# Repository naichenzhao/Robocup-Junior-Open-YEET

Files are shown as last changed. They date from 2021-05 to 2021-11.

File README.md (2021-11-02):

**Robocup Junior YEET**

These are the robot designs I created for Robocup Junior Open weight. 

These are my own creations and since I have graduated from the event, anyone rteading this is free to build off of any of my designs. My hope for this is to inspire others to build off of what I haev and use them to create even better concepts for the competition.

If you have any questions or concerns regarding the design, feel free to contact me:
- Twitter: https://twitter.com/N_zhao_
- Discord: https://discord.gg/ySBR4mmBkV

Included in the repo are:
- My 2020 design I planned on using for that year's competition - This is mostly tested but never created
- My 2021 design Which is pureley theoretical. It is a modefied version of the 2020 design built around a 20cm diameter

**2020 Design:**
This is the robot I planned on using for the 2020 competition (Which was cancelled due to covid). Some parts of the robot were tested but it was never completed as production stopped when the competition was cancelled

The specs of the robot are:
- 2x Teensy 4.0
- 1x Teensy 3.5
- 1x Open MV H7 (Omnidirectional mirror)
- 1x Spinning LIDAR
- 1x Bluetooth module
- 1x BNO-055 Accelerometer
- 2x Dribbler
- 2x Directional Kicker (I created models using both slider and geneva methods)
- 32x Photoresistors w/ LEDs (Controlled by 2 multiplexers)
- 12x Buttons w/ LEDs
- 2x IR laser module

**2021 Design:**
This is a robot built for the 2021 competition but since there is a significant chance that the competition will be cancalled, I have decided to thus release all of the robot files. This design is a smaller version built around the 2020 design created around a 20cm diameter instead of a 22 cm diameter

The specs of the robot are:
- 2x Teensy 4.0
- 1x Teensy 4.1
- 1x Open MV H7 (Omnidirectional mirror)
- 1x Spinning LIDAR
- 1x Bluetooth module
- 1x BNO-055 Accelerometer
- 2x Dribbler
- 2x Kicker
- 32x Photoresistors w/ LEDs (Controlled by 2 multiplexers)
- 8x Buttons w/ LEDs (Intead of individual LEDs, I am using a neopixel strip to conserve pins)
- 2x IR laser module

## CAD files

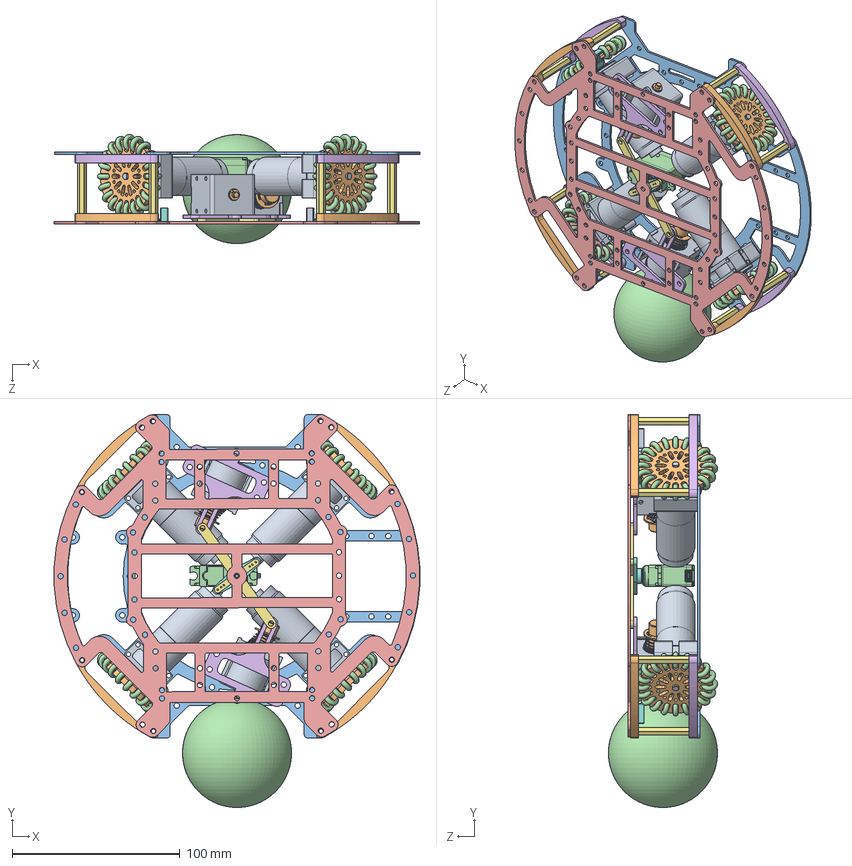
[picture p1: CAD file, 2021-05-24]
2020/Aimbot/Aimbot Test.SLDASM
217.9 x 234.3 x 65.1 mm
Open Motor x 4
50全向轮毂1 x 4
50全向轮小轴 x 80
50全向轮小轮 x 80
50全向轮毂2 x 4
Wheel Guard 4 x 4
M3X30-SCu x 8
Laser Left NH x 2
Laser Right NH x 2
Wheel Guard 5 x 4
Bot
球
Aimbot Mid
Aimbot Swing x 2
Aimbot Lever
Sero Adaptor
Part5^w_cb1029A x 2
Part1^w_cb1029A_pl x 2
w_21053081 x 2
Servo 2

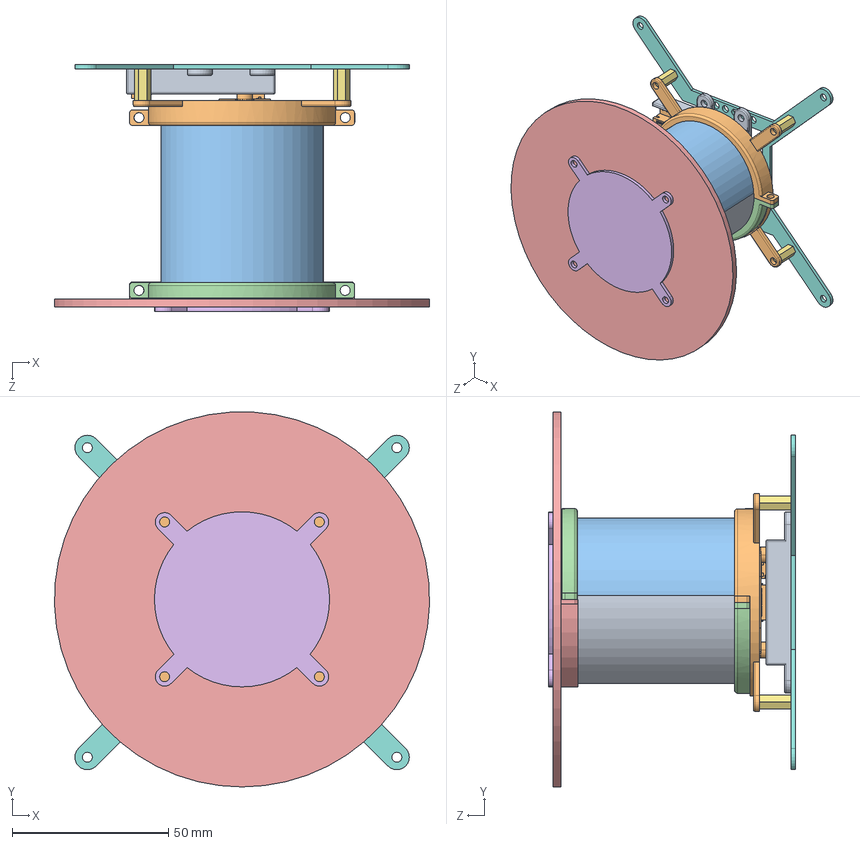
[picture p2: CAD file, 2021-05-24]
2021/Camera/Camera Module.SLDASM
119.9 x 119.9 x 79.0 mm
DCam 2
Open MV
镜筒
camera lock x 2
NH Top Cover V5
Mirror Adaptor
10mm Standoff x 4
Open Cam 1 - V2
Tube
Open Cam 2

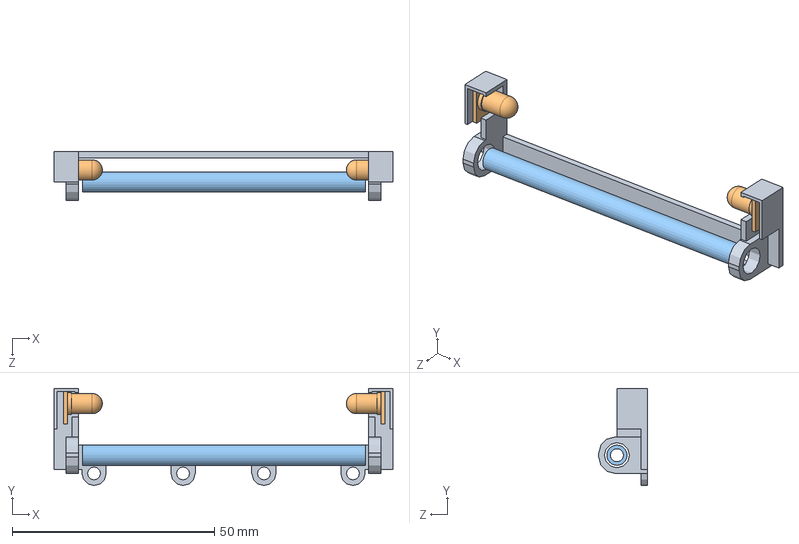
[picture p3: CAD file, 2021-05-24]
2021/Laser Module/Laser-Roller Assembly.SLDASM
83.8 x 24.0 x 12.0 mm
Laser - Roller module
IR Laser Diode x 2
Roller Bar

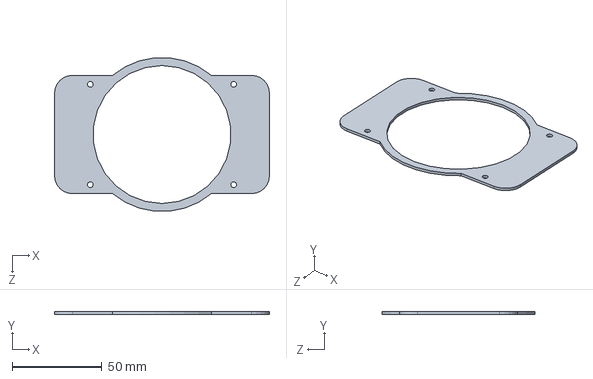
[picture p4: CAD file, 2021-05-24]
2021/PCB - Solidworks/Main PCB.SLDPRT
120.0 x 1.50 x 85.6 mm

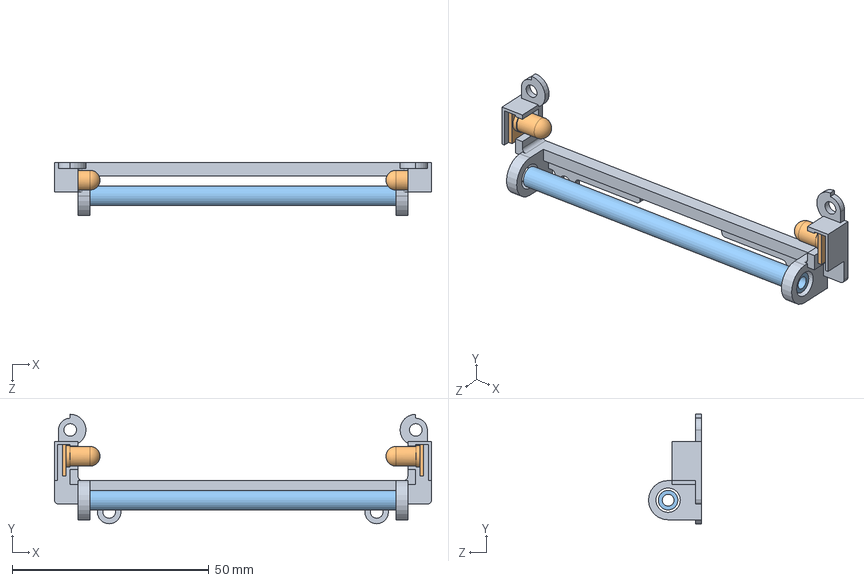
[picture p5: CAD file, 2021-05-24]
2020/Laser Module/Laser + Roller Assembly.SLDASM
95.8 x 27.9 x 13.5 mm
Laser Module
IR Laser Diode x 2
Roller Rod

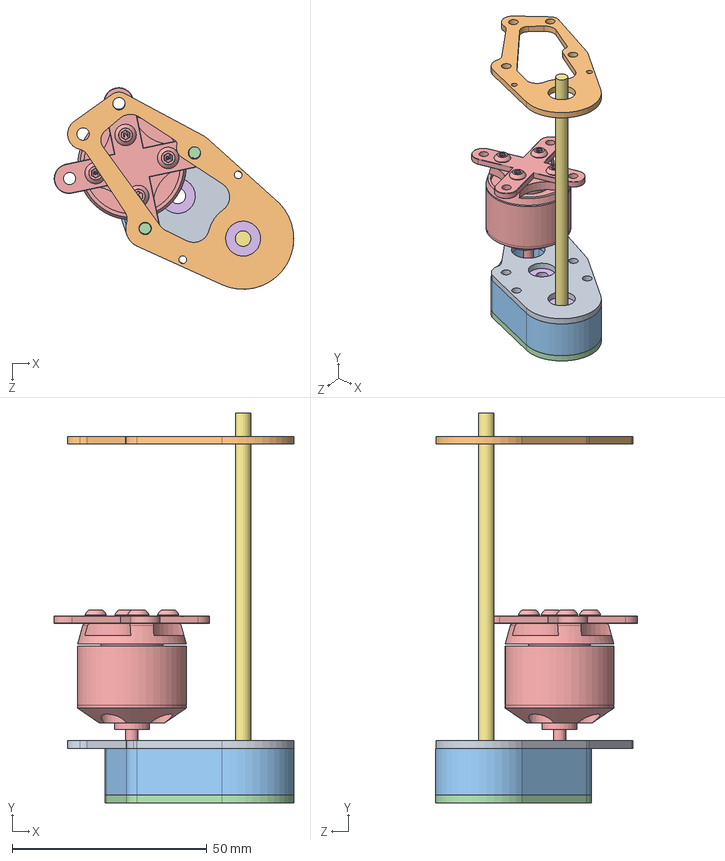
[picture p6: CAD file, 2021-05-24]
2020/Dribbler/Dribbler200.SLDASM
61.4 x 100.0 x 51.7 mm
Dribbler 201
Dribbler 202
Dribbler 203
Dribbler 204
Motor
Large Gear x 2
Dribbler Rod

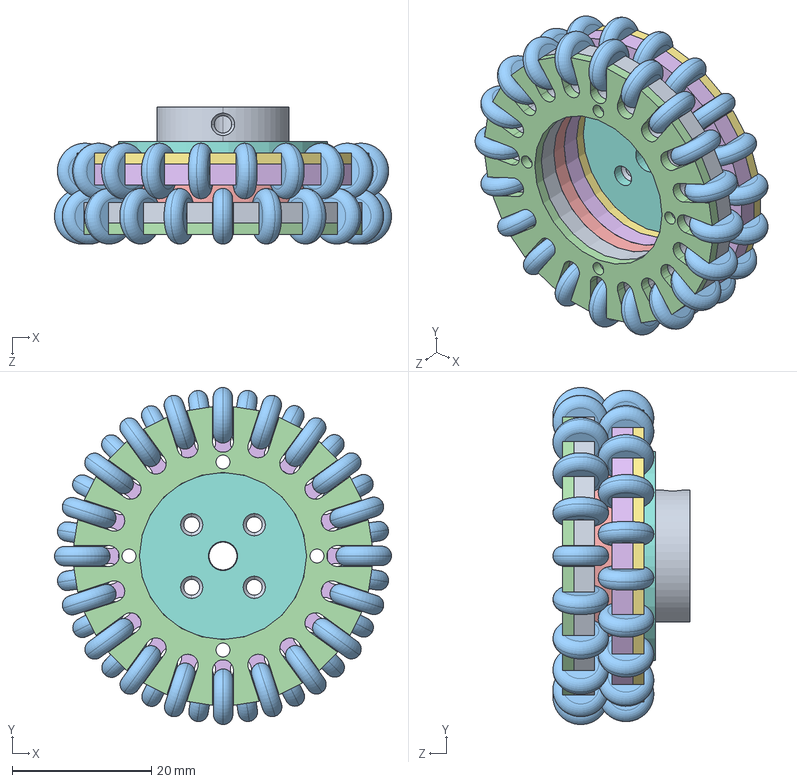
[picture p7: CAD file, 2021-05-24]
2020/Wheel/Wheel 2.0.SLDASM
48.4 x 48.4 x 19.7 mm
Wheel Plate 2.2
Wheel 2.0 Ring x 2
Inner Wheel - GTF x 40
Wheel Plate 2.1
Spacer 2.0
Wheel Plate 2.4
Wheel Plate 2.3
Cross 2.0
Wheel Mounting

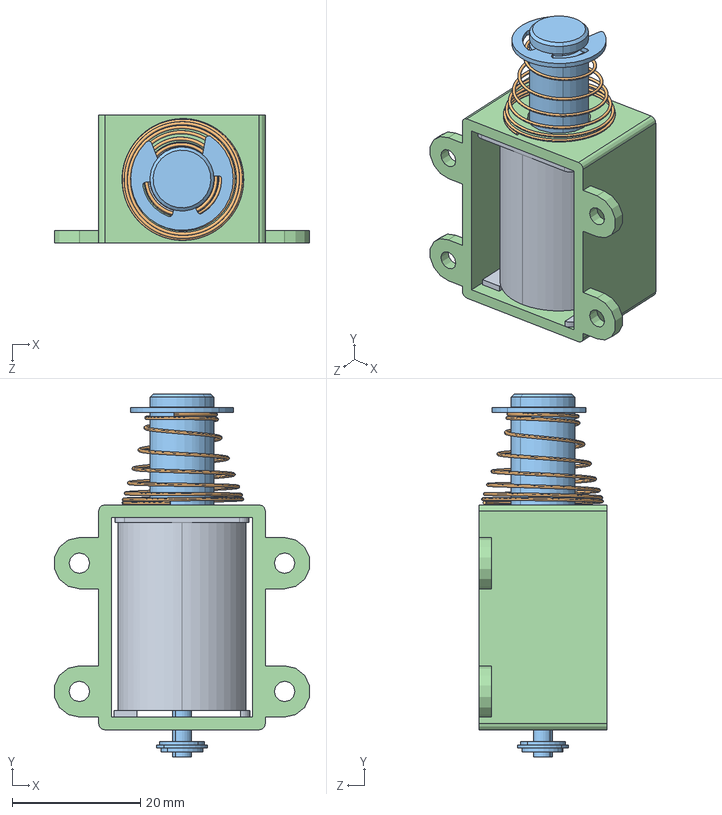
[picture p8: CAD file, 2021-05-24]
2021/New Kicker/Kicker Assembly.SLDASM
39.8 x 56.6 x 20.0 mm
Kicker Solenoid Core
Kicker Spring
Kicker Core
kicker Shell

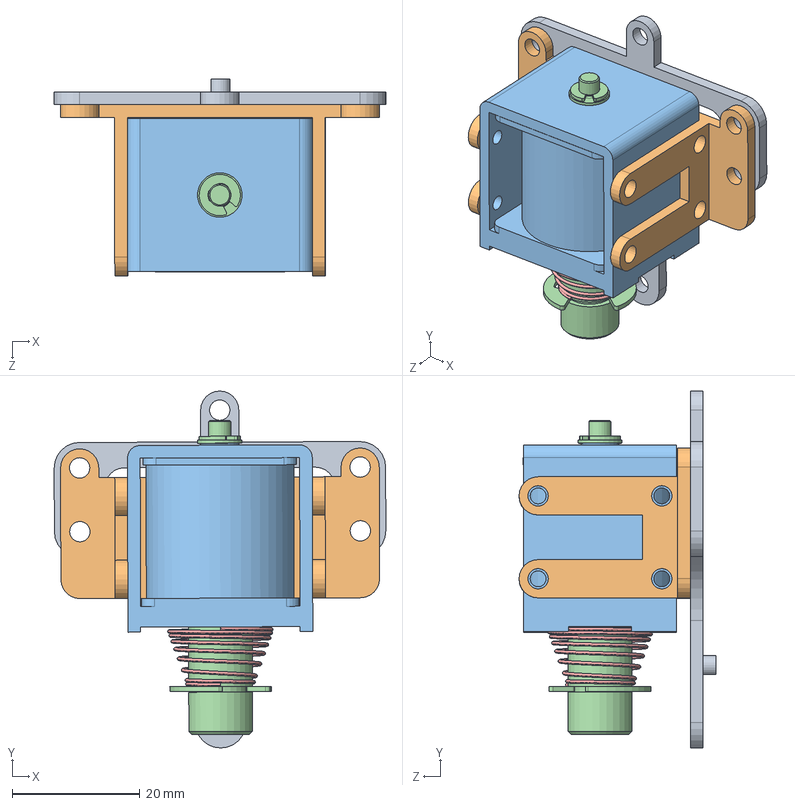
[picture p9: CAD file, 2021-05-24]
2020/Aimbot/Aimbot-S Swing.SLDASM
52.0 x 56.0 x 30.9 mm
Aimbot Swing
CB1029 Kicker Stand
Part5^w_cb1029A
Part1^w_cb1029A_pl
w_21053081

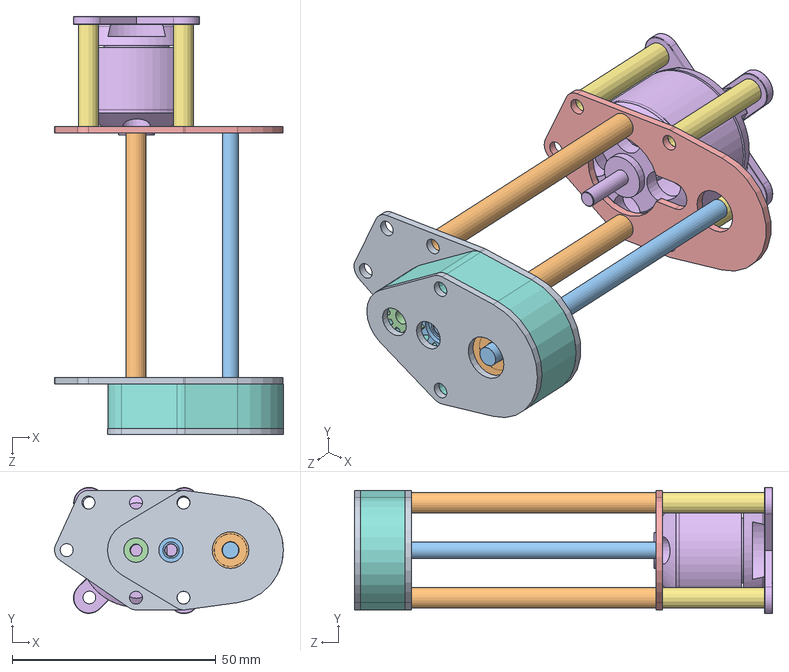
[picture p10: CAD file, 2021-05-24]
2021/Mini Dribbler/Mini Dribbler Assembly.SLDASM
56.2 x 31.0 x 102.7 mm
Mini Dribbler Plate 1
front - Gear
mid-gear
BrushlessGear
Mini Dribbler Plate3
Stand
25mm - pole x 3
Mini Dribbler wall
Mini Dribbler Plate 2
60mm - pole x 2
Rod

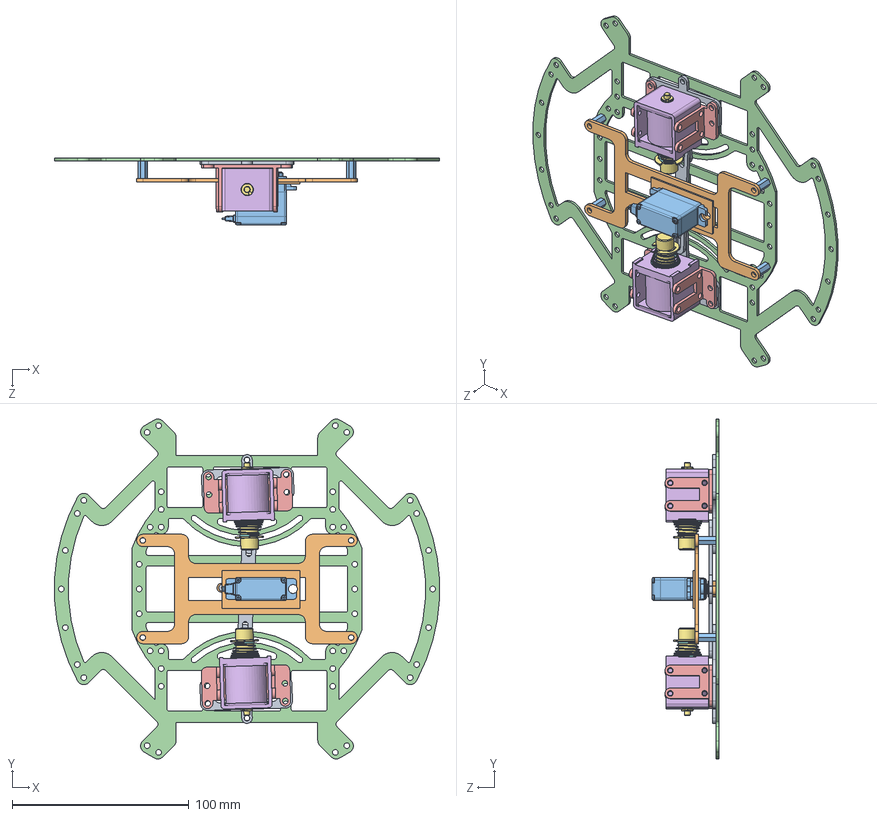
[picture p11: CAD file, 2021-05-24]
2020/Aimbot/Aimbot-S Test.SLDASM
217.7 x 192.2 x 37.6 mm
Aimbot Swing x 2
Sero Adaptor
Servo 2
Aimbot Mid
CB1029 Kicker Stand x 2
Part5^w_cb1029A x 2
Part1^w_cb1029A_pl x 2
w_21053081 x 2
Aimbot Lever
Servo Stand
10mm Standoff x 4

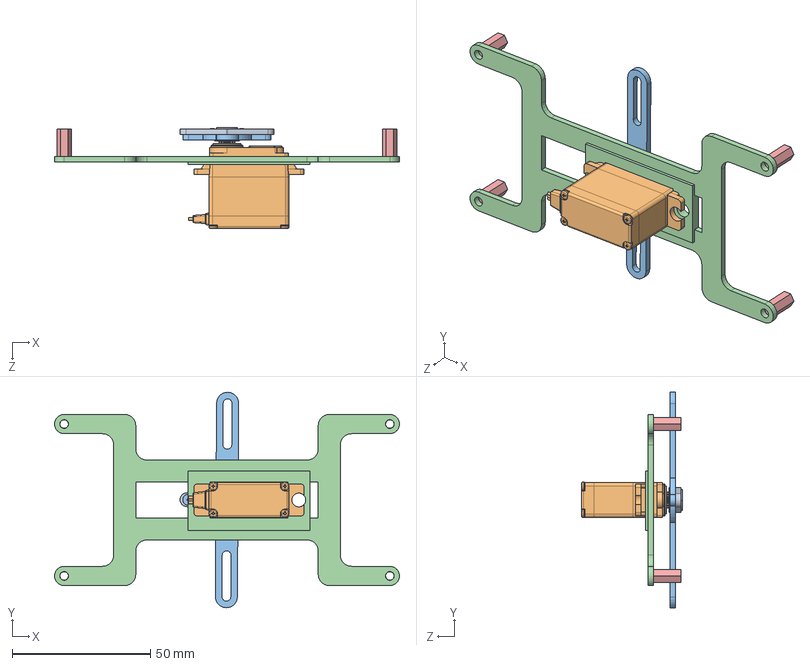
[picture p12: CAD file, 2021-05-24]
2020/Aimbot/Aimbot-S Pivot.SLDASM
124.8 x 78.0 x 36.6 mm
Sero Adaptor
Servo 2
Aimbot Lever
Servo Stand
10mm Standoff x 4

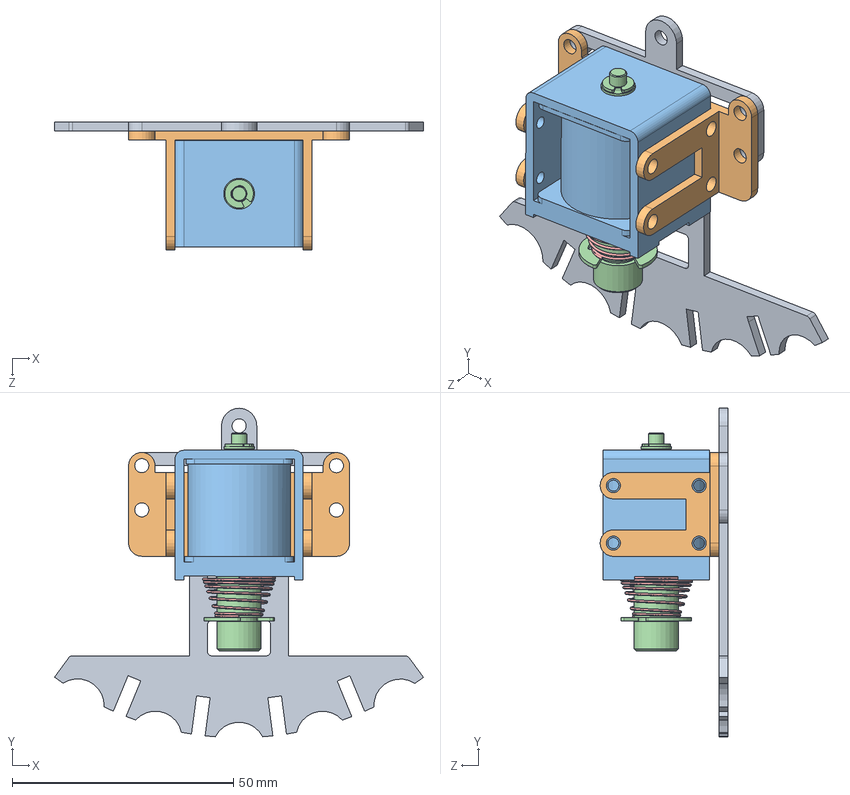
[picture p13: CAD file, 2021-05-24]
2020/Aimbot/Aimbot-G Swing.SLDASM
83.4 x 74.3 x 28.9 mm
Aimbot Geneva 1
CB1029 Kicker Stand
Part5^w_cb1029A
Part1^w_cb1029A_pl
w_21053081

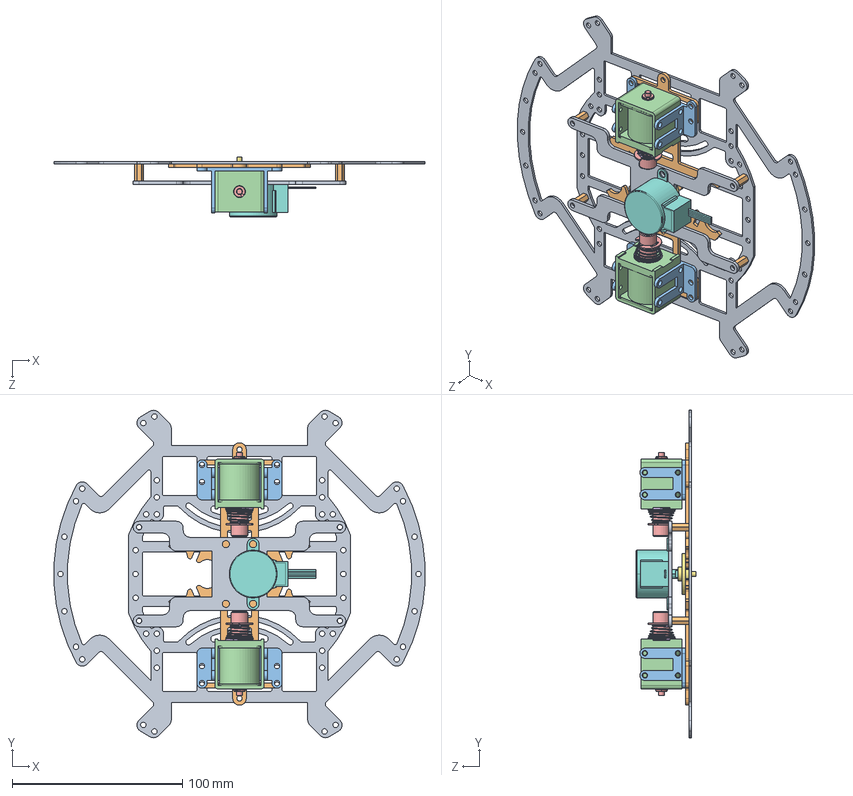
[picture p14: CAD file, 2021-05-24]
2020/Aimbot/Aimbot-G Test.SLDASM
217.7 x 192.2 x 35.0 mm
Aimbot Mid
Aimbot Geneva 1 x 2
CB1029 Kicker Stand x 2
Part5^w_cb1029A x 2
Part1^w_cb1029A_pl x 2
w_21053081 x 2
Aimbot Geneva 2
Stepper Motor
Stepper Stand
10mm Standoff x 4

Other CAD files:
2021/Wheel/Wheel 2.0.SLDASM
2020/Aimbot/Aimbot-G Pivot.SLDASM
2020/Camera/NH Top Cover V5.SLDPRT
2020/Aimbot/Aimbot Geneva 1.SLDPRT
2020/Aimbot/Aimbot Geneva 2.SLDPRT
2020/Aimbot/Aimbot Lever V2.SLDPRT
2020/Aimbot/Aimbot Lever.SLDPRT
2020/Aimbot/Aimbot Mid.SLDPRT
2020/Aimbot/Aimbot Swing + Kicker.SLDPRT
2020/Aimbot/Aimbot Swing.SLDPRT
2020/Aimbot/Sero Adaptor.SLDPRT
2020/Aimbot/Servo 2.SLDPRT
2020/Aimbot/Servo Stand V2.SLDPRT
2020/Aimbot/Servo Stand.SLDPRT
2020/Aimbot/Servo.SLDPRT
2020/Aimbot/Stepper Motor.SLDPRT
2020/Aimbot/Stepper Stand.SLDPRT
2020/Camera/Mirror Adaptor.SLDPRT
2020/Camera/Open Cam 1 - V2.SLDPRT
2020/Camera/Open Cam 1.SLDPRT
2020/Camera/Open Cam 2.SLDPRT
2020/Camera/Tube.SLDPRT
2020/Camera/camera lock.SLDPRT
2020/Dribbler/Dribbler 201.SLDPRT
2020/Dribbler/Dribbler 202.SLDPRT
2020/Dribbler/Dribbler 203.SLDPRT
2020/Dribbler/Dribbler 204.SLDPRT
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

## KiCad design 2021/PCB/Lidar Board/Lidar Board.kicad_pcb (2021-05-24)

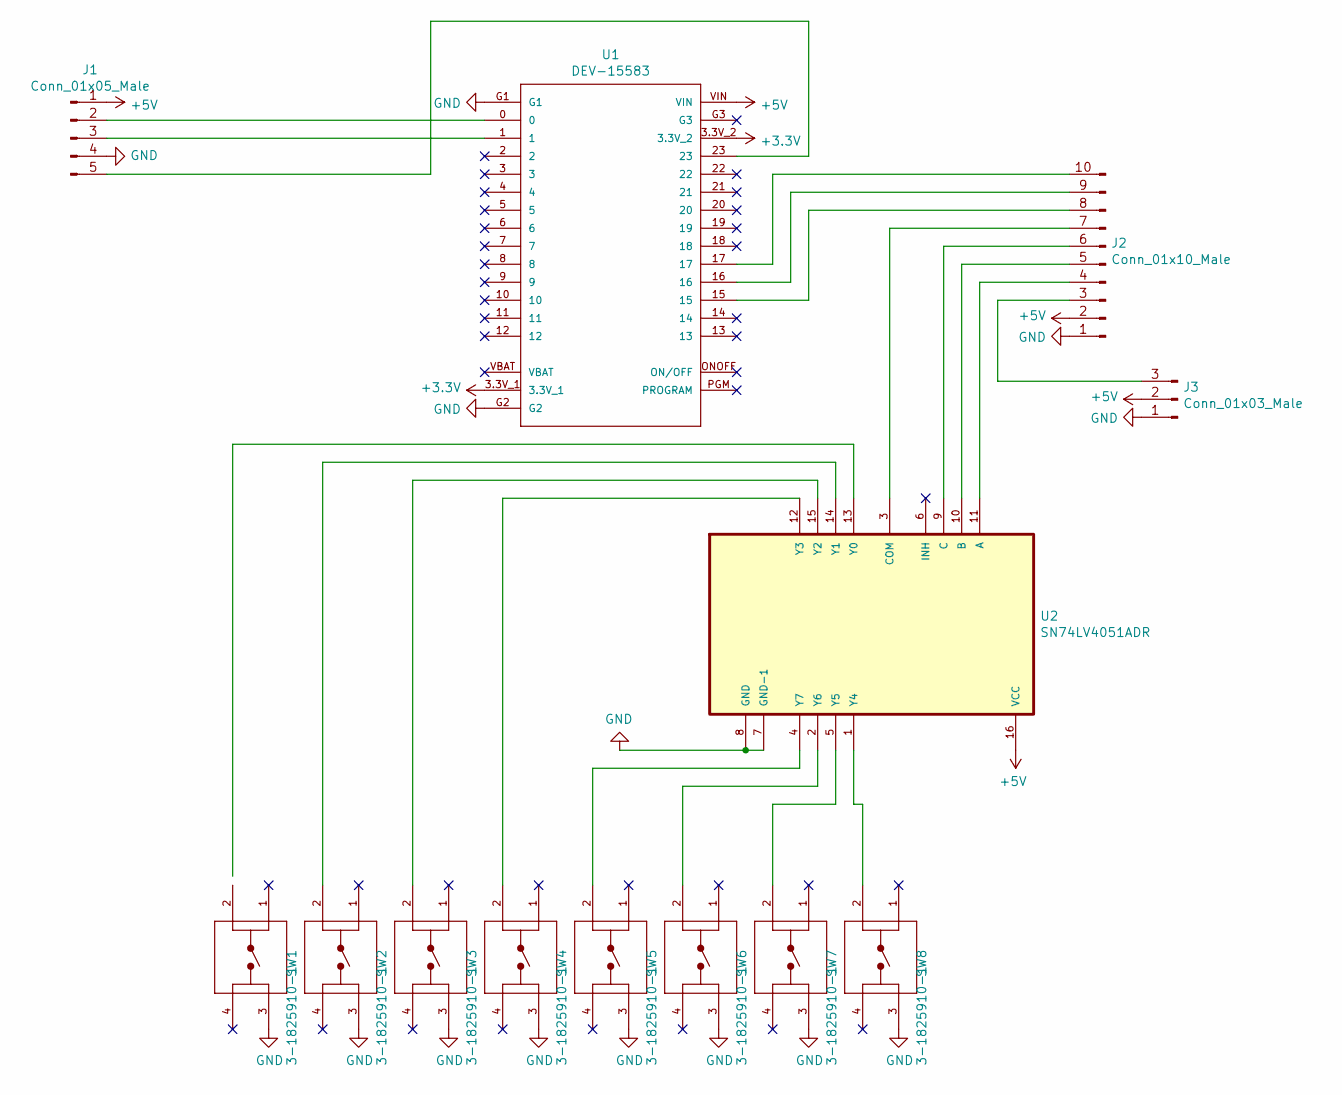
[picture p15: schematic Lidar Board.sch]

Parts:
J1: Conn_01x05_Male; PinHeader_1x05_P2.54mm_Vertical
J2: Conn_01x10_Male; PinHeader_1x10_P2.54mm_Vertical
J3: Conn_01x03_Male; PinHeader_1x03_P2.54mm_Vertical
SW1, SW2, SW3, SW4, SW5, SW6, SW7, SW8: 3-1825910-1; TE_3-1825910-1
U1: DEV-15583; MODULE_DEV-15583
U2: SN74LV4051ADR; SOIC127P600X175-16N

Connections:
+3V3: U1.3.3V_1, U1.3.3V_2
+5V: J1.1, J2.2, J3.2, U1.VIN, U2.16 (VCC)
GND: J1.4, J2.1, J3.1, SW1.3, SW2.3, SW3.3, SW4.3, SW5.3, SW6.3, SW7.3, SW8.3, U1.G1, U1.G2, U2.7 (GND-1), U2.8 (GND)
unnamed: J1.2, U1.0
unnamed: J1.3, U1.1
unnamed: J1.5, U1.23
unnamed: J2.3, J3.3
unnamed: J2.4, U2.11 (A)
unnamed: J2.5, U2.10 (B)
unnamed: J2.6, U2.9 (C)
unnamed: J2.7, U2.3 (COM)
unnamed: J2.8, U1.15
unnamed: J2.9, U1.16
unnamed: J2.10, U1.17
unnamed: SW2.2, U2.14 (Y1)
unnamed: SW3.2, U2.15 (Y2)
unnamed: SW4.2, U2.12 (Y3)
unnamed: SW5.2, U2.4 (Y7)
unnamed: SW6.2, U2.2 (Y6)
unnamed: SW7.2, U2.5 (Y5)
unnamed: SW8.2, U2.1 (Y4)

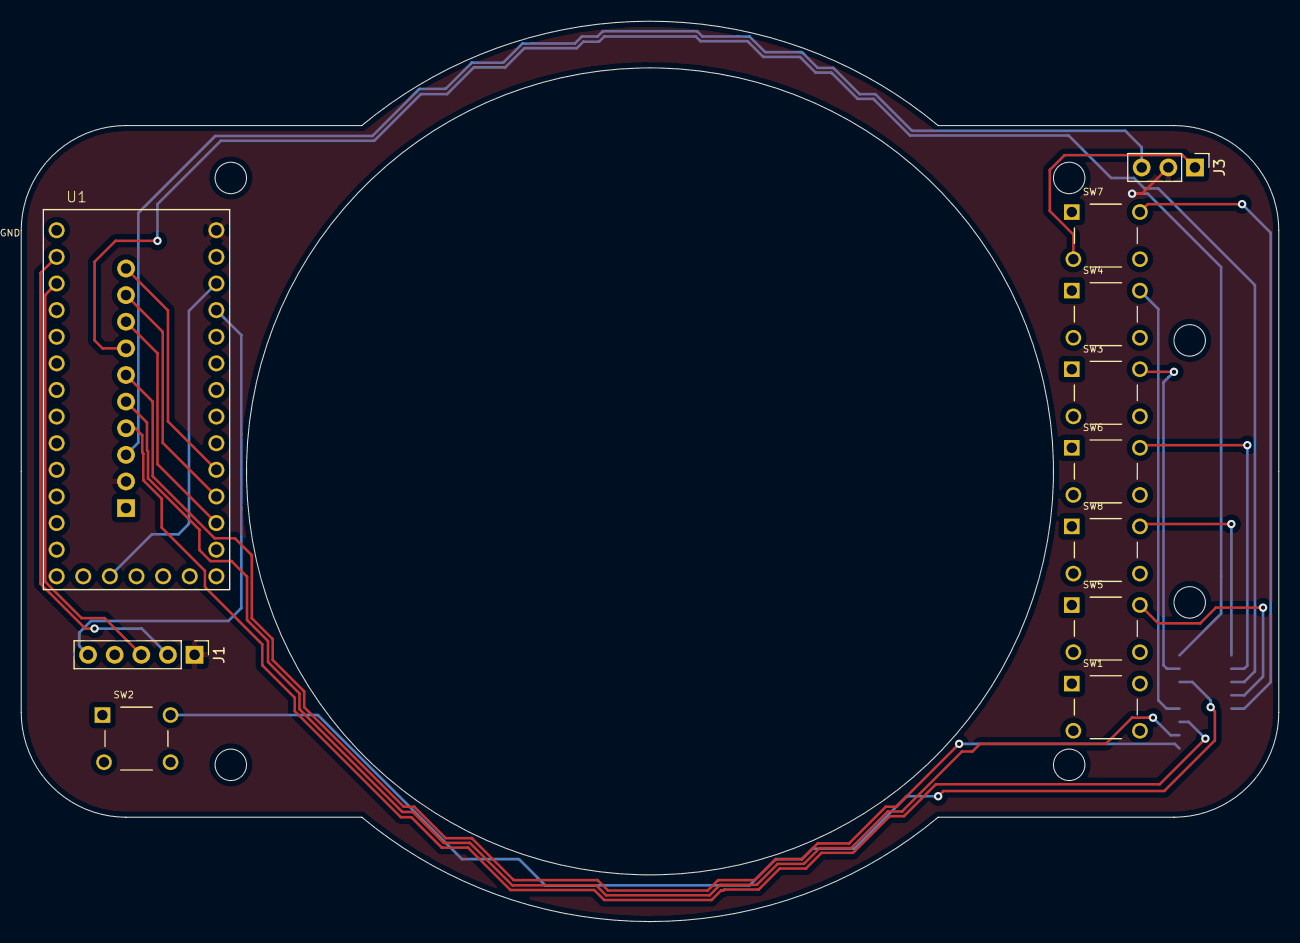
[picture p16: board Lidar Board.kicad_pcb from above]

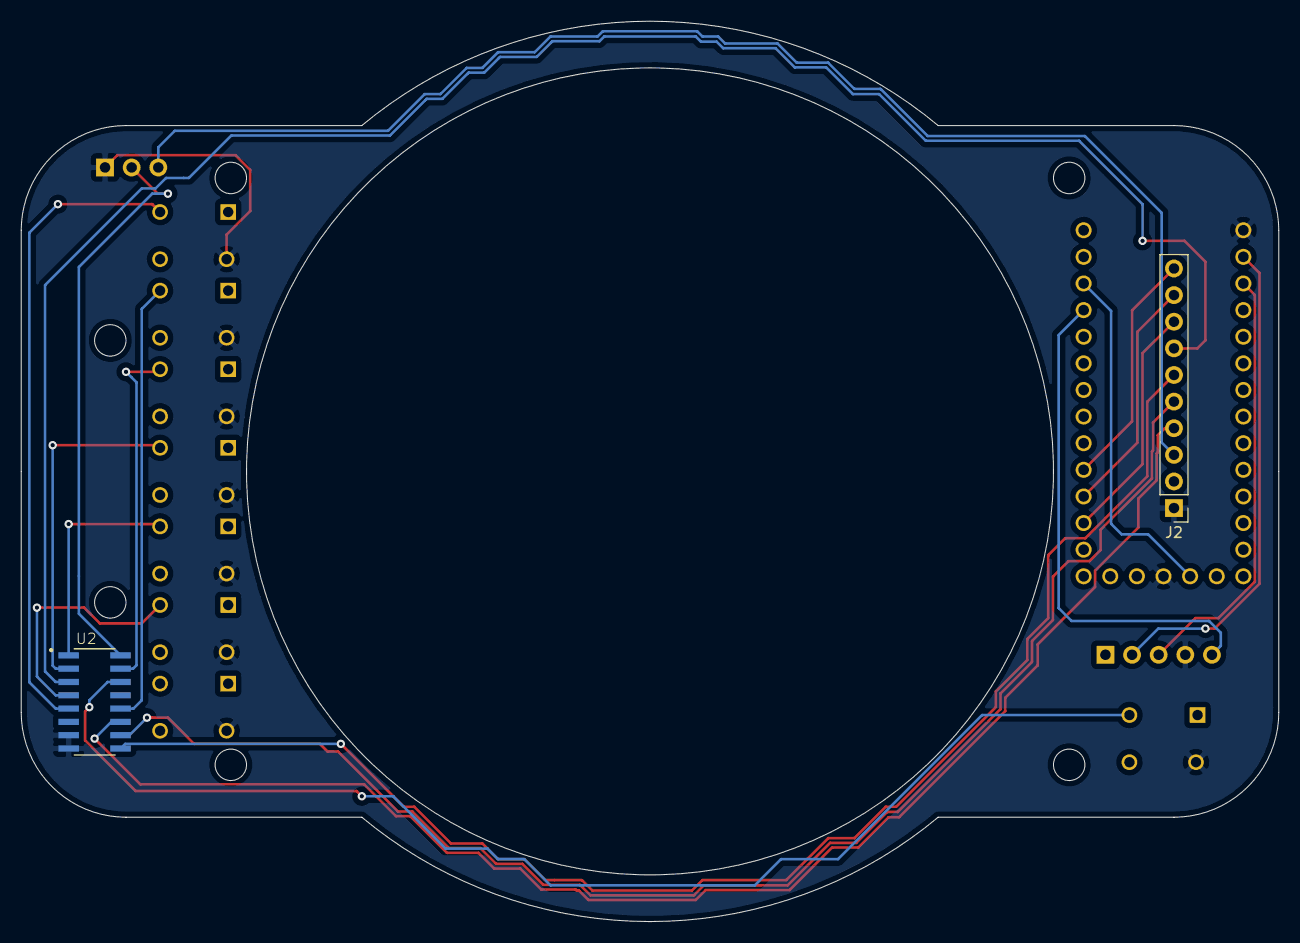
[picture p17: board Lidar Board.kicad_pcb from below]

Board: 2 copper layers, 120.0 x 85.9 mm, 13 parts (2 on the bottom side), 21 nets.

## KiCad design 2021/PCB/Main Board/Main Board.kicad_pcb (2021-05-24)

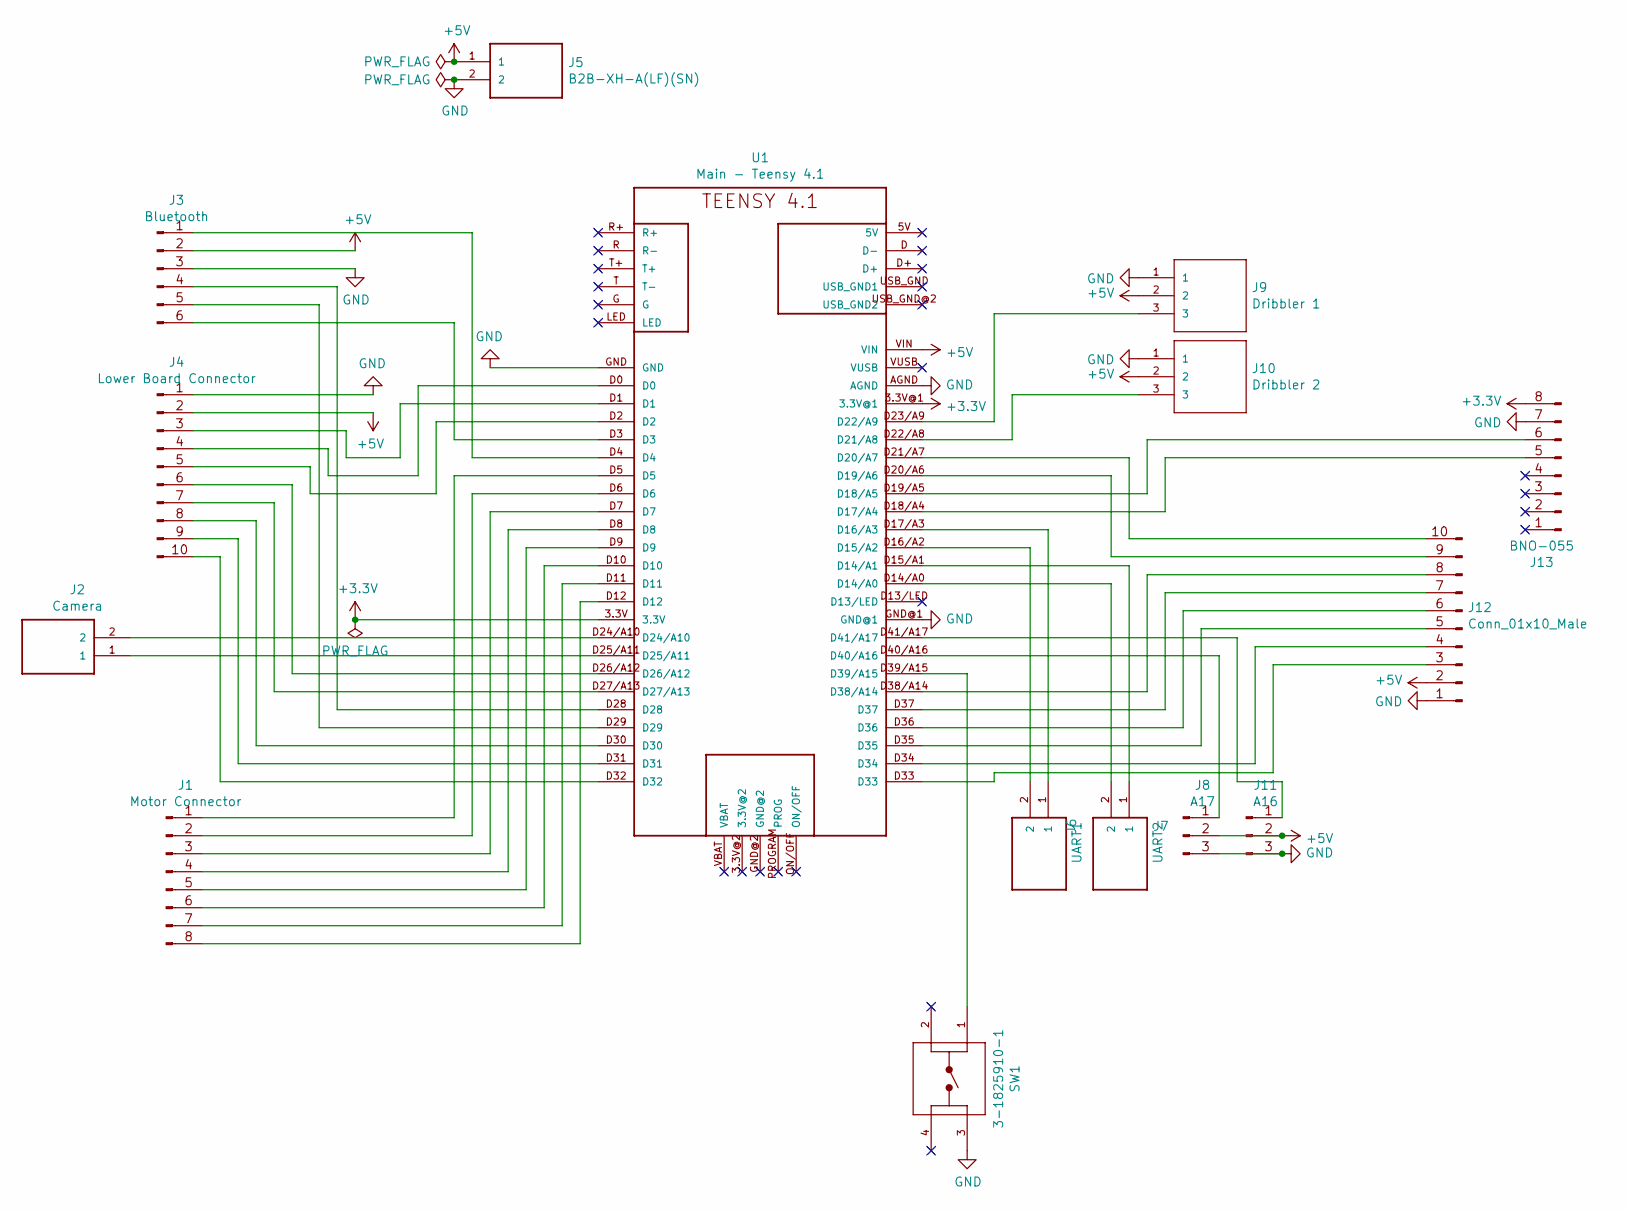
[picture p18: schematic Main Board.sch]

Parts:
J1: Motor Connector; Stocko_MKS_1658-6-0-808_1x8_P2.50mm_Vertical
J2: Camera; JST_EH_B2B-EH-A_1x02_P2.50mm_Vertical
J3: Bluetooth; Stocko_MKS_1656-6-0-606_1x6_P2.50mm_Vertical
J4: Lower Board Connector; JST_XH_B10B-XH-AM_1x10_P2.50mm_Vertical
J5: B2B-XH-A(LF)(SN); JST_EH_B2B-EH-A_1x02_P2.50mm_Vertical
J6: UART1; JST_EH_B2B-EH-A_1x02_P2.50mm_Vertical
J7: UART2; JST_EH_B2B-EH-A_1x02_P2.50mm_Vertical
J8: A17; JST_EH_B3B-EH-A_1x03_P2.50mm_Vertical
J9: Dribbler 1; JST_EH_B3B-EH-A_1x03_P2.50mm_Vertical
J10: Dribbler 2; JST_EH_B3B-EH-A_1x03_P2.50mm_Vertical
J11: A16; JST_EH_B3B-EH-A_1x03_P2.50mm_Vertical
J12: Conn_01x10_Male; JST_XH_B10B-XH-AM_1x10_P2.50mm_Vertical
J13: BNO-055; PinHeader_1x08_P2.54mm_Vertical
SW1: 3-1825910-1; TE_3-1825910-1
U1: Main - Teensy 4.1; DEV-16771

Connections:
+3V3: J13.8, U1.3.3V, U1.3.3V@1
+5V: J3.2, J4.2, J5.1, J8.2, J9.2, J10.2, J11.2, J12.2, U1.VIN
GND: J3.3, J4.1, J5.2, J8.3, J9.1, J10.1, J11.3, J12.1, J13.7, SW1.3, U1.AGND, U1.GND, U1.GND@1
unnamed: J1.1, U1.D5
unnamed: J1.2, U1.D6
unnamed: J1.3, U1.D7
unnamed: J1.4, U1.D8
unnamed: J1.5, U1.D9
unnamed: J1.6, U1.D10
unnamed: J1.7, U1.D11
unnamed: J1.8, U1.D12
unnamed: J2.1, U1.D25/A11
unnamed: J2.2, U1.D24/A10
unnamed: J3.1, U1.D4
unnamed: J3.4, U1.D28
unnamed: J3.5, U1.D29
unnamed: J3.6, U1.D3
unnamed: J4.3, U1.D1
unnamed: J4.4, U1.D0
unnamed: J4.5, U1.D2
unnamed: J4.6, U1.D26/A12
unnamed: J4.7, U1.D27/A13
unnamed: J4.8, U1.D30
unnamed: J4.9, U1.D31
unnamed: J4.10, U1.D32
unnamed: J6.1, U1.D17/A3 (D16/A3)
unnamed: J6.2, U1.D16/A2 (D15/A2)
unnamed: J7.1, U1.D15/A1 (D14/A1)
unnamed: J7.2, U1.D14/A0
unnamed: J8.1, U1.D40/A16
unnamed: J9.3, U1.D23/A9 (D22/A9)
unnamed: J10.3, U1.D22/A8 (D21/A8)
unnamed: J11.1, U1.D41/A17
unnamed: J12.3, U1.D33
unnamed: J12.4, U1.D34
unnamed: J12.5, U1.D35
unnamed: J12.6, U1.D36
unnamed: J12.7, U1.D37
unnamed: J12.8, U1.D38/A14
unnamed: J12.9, U1.D20/A6 (D19/A6)
unnamed: J12.10, U1.D21/A7 (D20/A7)
unnamed: J13.5, U1.D18/A4 (D17/A4)
unnamed: J13.6, U1.D19/A5 (D18/A5)
unnamed: SW1.1, U1.D39/A15

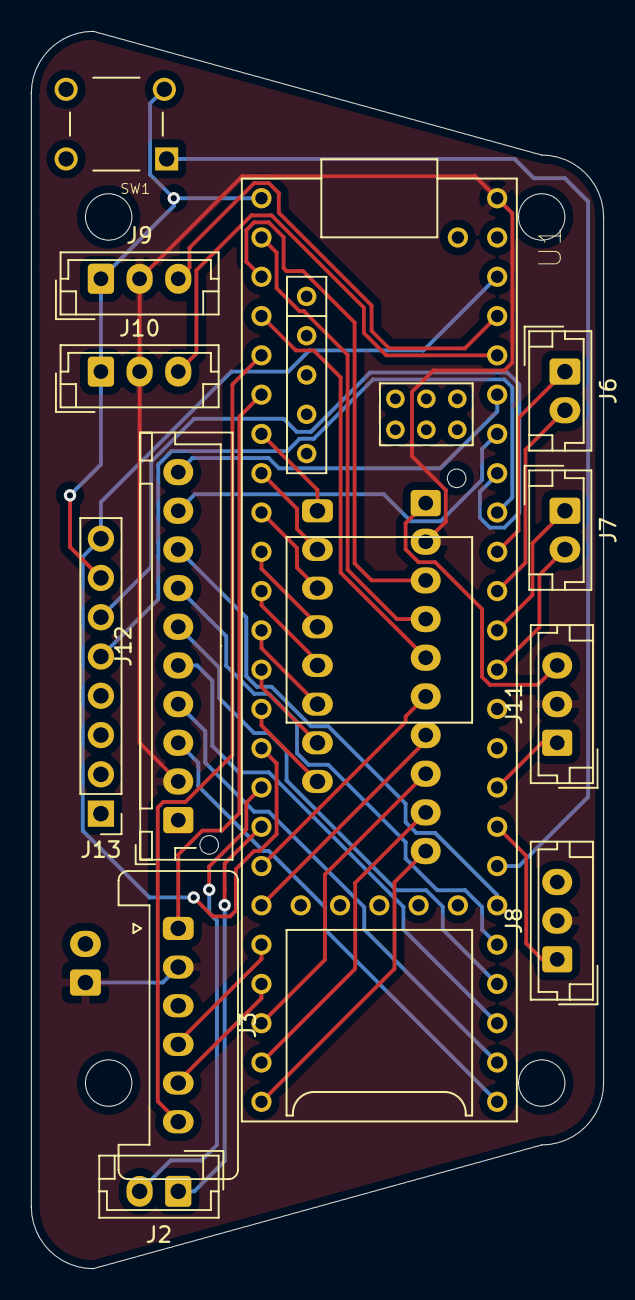
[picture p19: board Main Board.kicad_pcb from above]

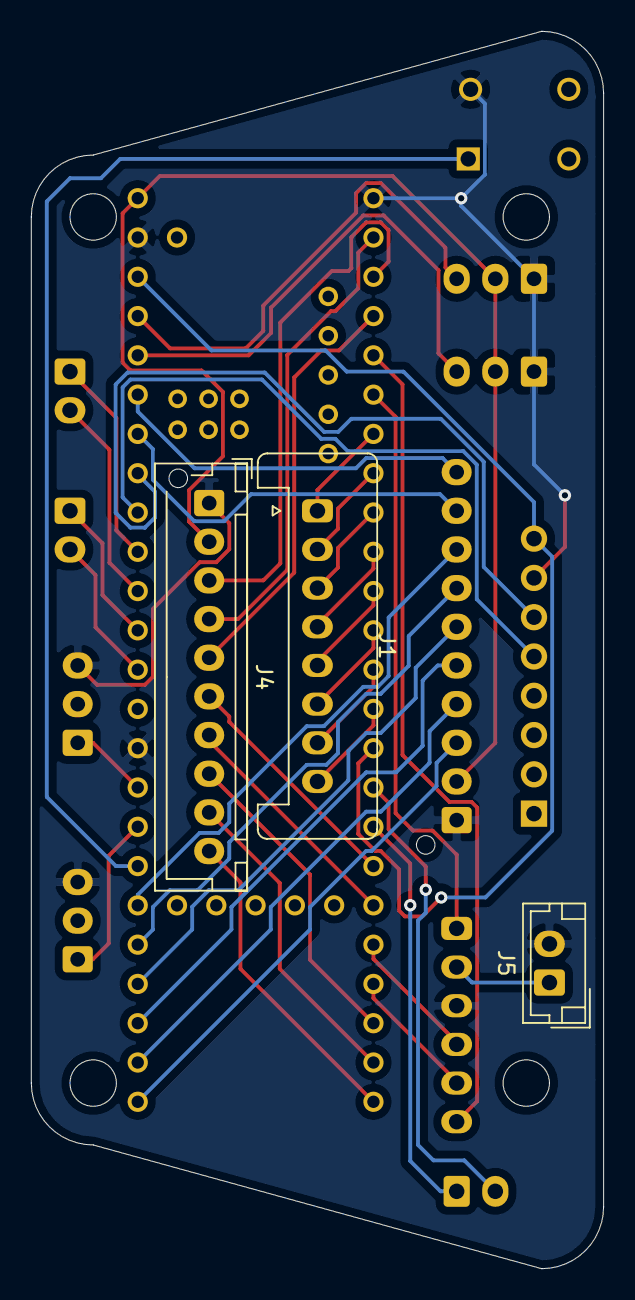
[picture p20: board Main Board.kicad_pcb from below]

Board: 2 copper layers, 37.0 x 80.0 mm, 15 parts (3 on the bottom side), 44 nets.

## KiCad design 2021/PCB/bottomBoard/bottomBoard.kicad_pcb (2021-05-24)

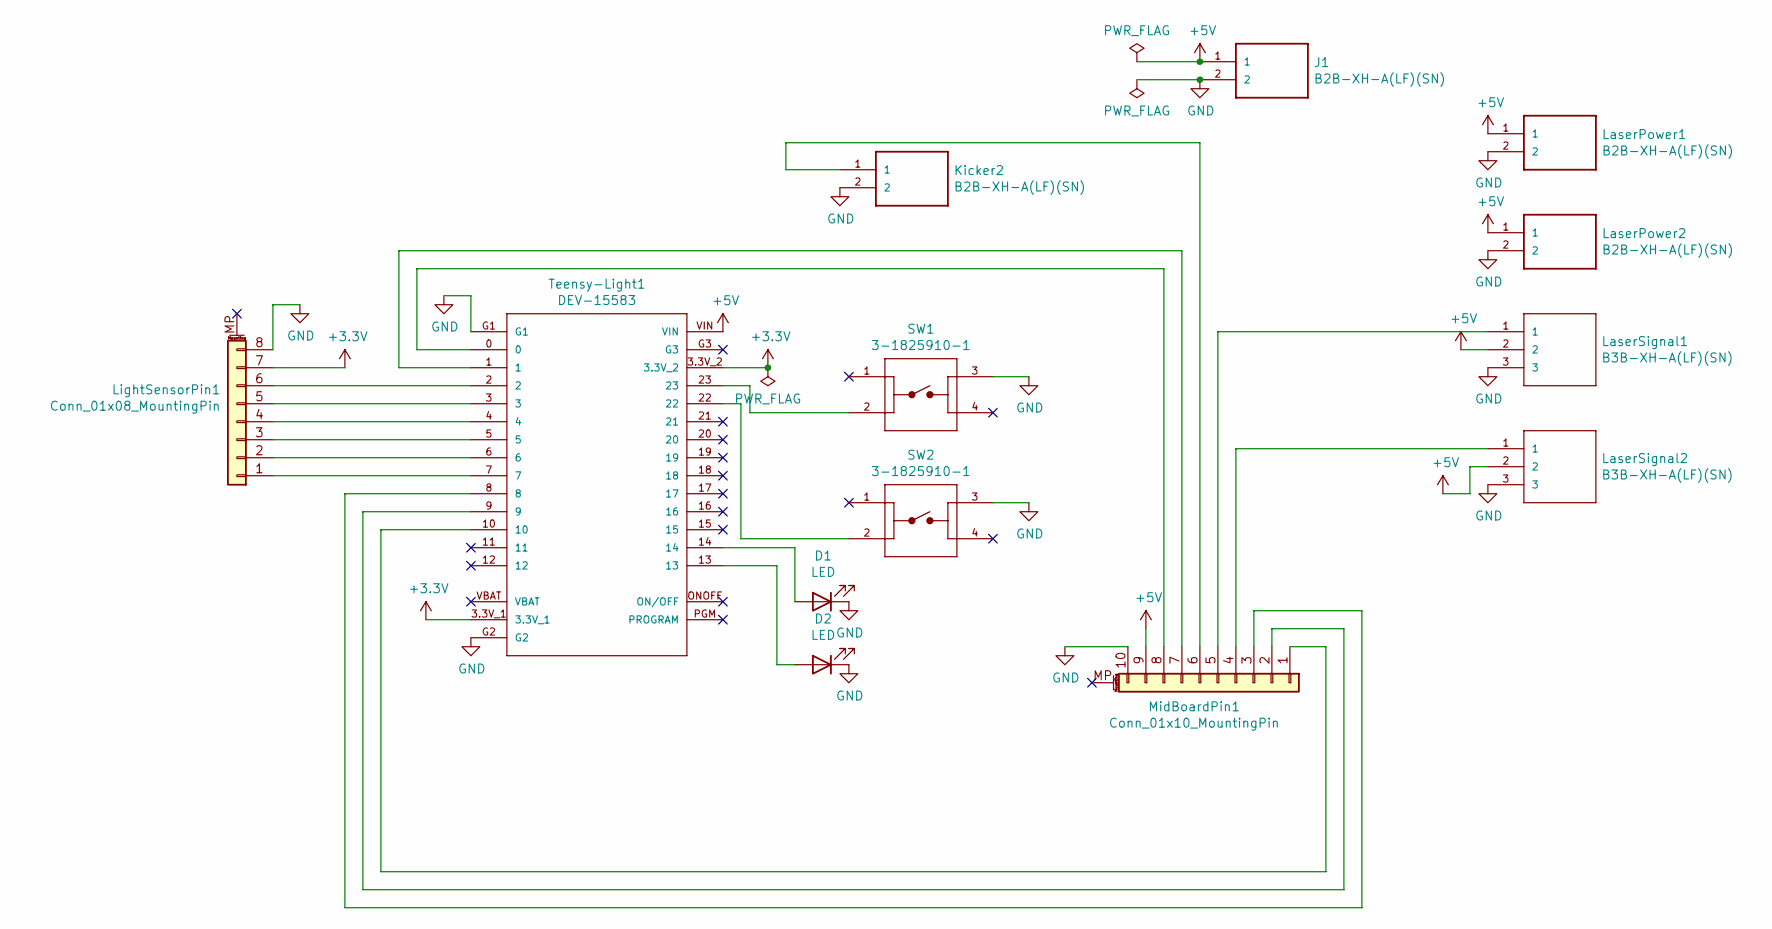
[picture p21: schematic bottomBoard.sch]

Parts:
D1, D2: LED; C_1206_3216Metric
J1: B2B-XH-A(LF)(SN); JST_B2B-XH-A(LF)(SN)
Kicker2: B2B-XH-A(LF)(SN); JST_B2B-XH-A(LF)(SN)
LaserPower1, LaserPower2: B2B-XH-A(LF)(SN); JST_B2B-XH-A(LF)(SN)
LaserSignal1, LaserSignal2: B3B-XH-A(LF)(SN); JST_B3B-XH-A(LF)(SN)
LightSensorPin1: Conn_01x08_MountingPin; PinHeader_1x08_P2.54mm_Vertical
MidBoardPin1: Conn_01x10_MountingPin; PinHeader_1x10_P2.54mm_Vertical
SW1, SW2: 3-1825910-1; TE_3-1825910-1
Teensy-Light1: DEV-15583; MODULE_DEV-15583

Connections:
+3V3: LightSensorPin1.7, Teensy-Light1.3.3V_1, Teensy-Light1.3.3V_2
+5V: J1.1, LaserPower1.1, LaserPower2.1, LaserSignal1.2, LaserSignal2.2, MidBoardPin1.9, Teensy-Light1.VIN
GND: D1.1 (K), D2.1 (K), J1.2, Kicker2.2, LaserPower1.2, LaserPower2.2, LaserSignal1.3, LaserSignal2.3, LightSensorPin1.8, MidBoardPin1.10, SW1.3, SW2.3, Teensy-Light1.G1, Teensy-Light1.G2
unnamed: D1.2 (A), Teensy-Light1.14
unnamed: D2.2 (A), Teensy-Light1.13
unnamed: Kicker2.1, MidBoardPin1.6
unnamed: LaserSignal1.1, MidBoardPin1.5
unnamed: LaserSignal2.1, MidBoardPin1.4
unnamed: LightSensorPin1.1, Teensy-Light1.7
unnamed: LightSensorPin1.2, Teensy-Light1.6
unnamed: LightSensorPin1.3, Teensy-Light1.5
unnamed: LightSensorPin1.4, Teensy-Light1.4
unnamed: LightSensorPin1.5, Teensy-Light1.3
unnamed: LightSensorPin1.6, Teensy-Light1.2
unnamed: MidBoardPin1.1, Teensy-Light1.10
unnamed: MidBoardPin1.2, Teensy-Light1.9
unnamed: MidBoardPin1.3, Teensy-Light1.8
unnamed: MidBoardPin1.7, Teensy-Light1.1
unnamed: MidBoardPin1.8, Teensy-Light1.0
unnamed: SW1.2, Teensy-Light1.23
unnamed: SW2.2, Teensy-Light1.22

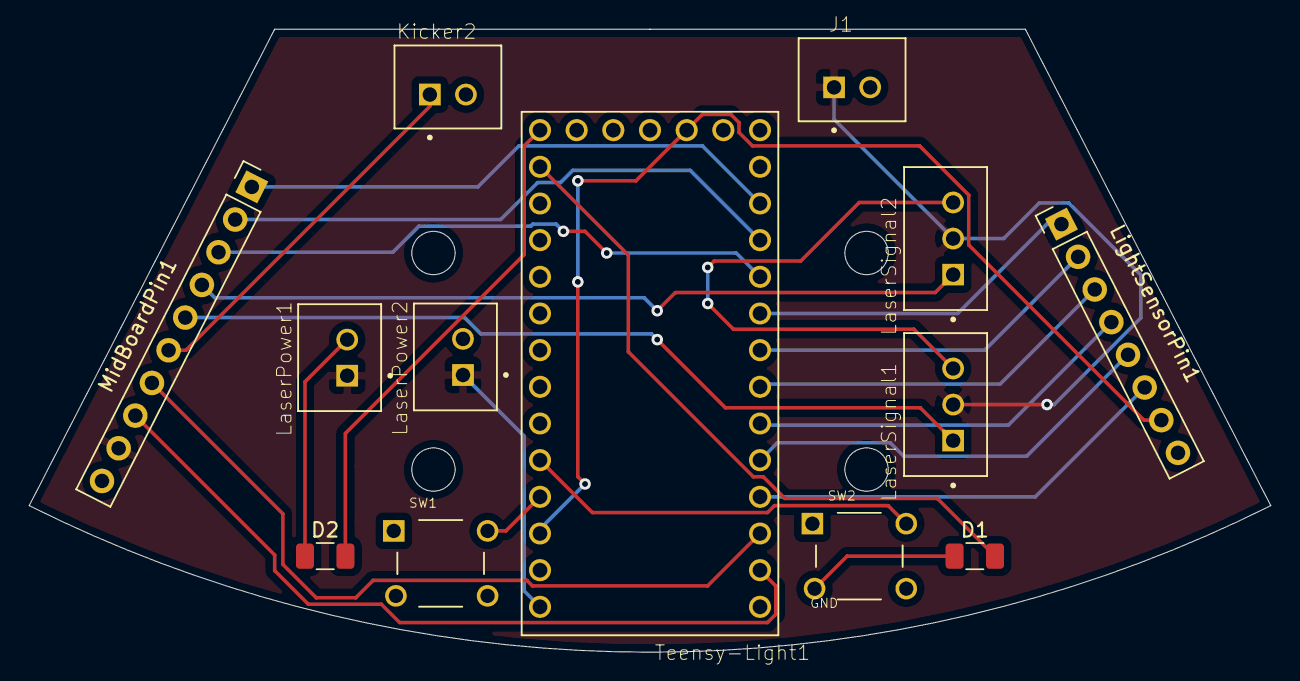
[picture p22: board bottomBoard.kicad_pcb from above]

Board: 2 copper layers, 86.0 x 43.2 mm, 13 parts (0 on the bottom side), 21 nets.

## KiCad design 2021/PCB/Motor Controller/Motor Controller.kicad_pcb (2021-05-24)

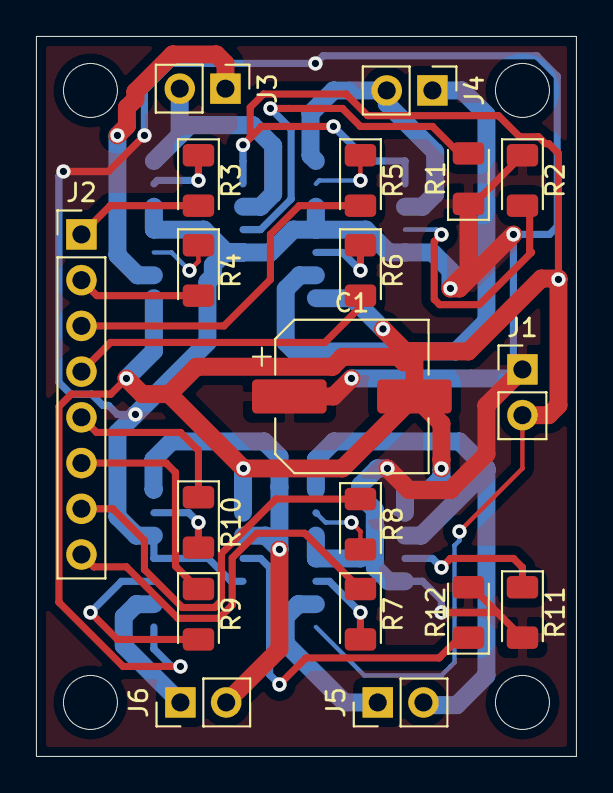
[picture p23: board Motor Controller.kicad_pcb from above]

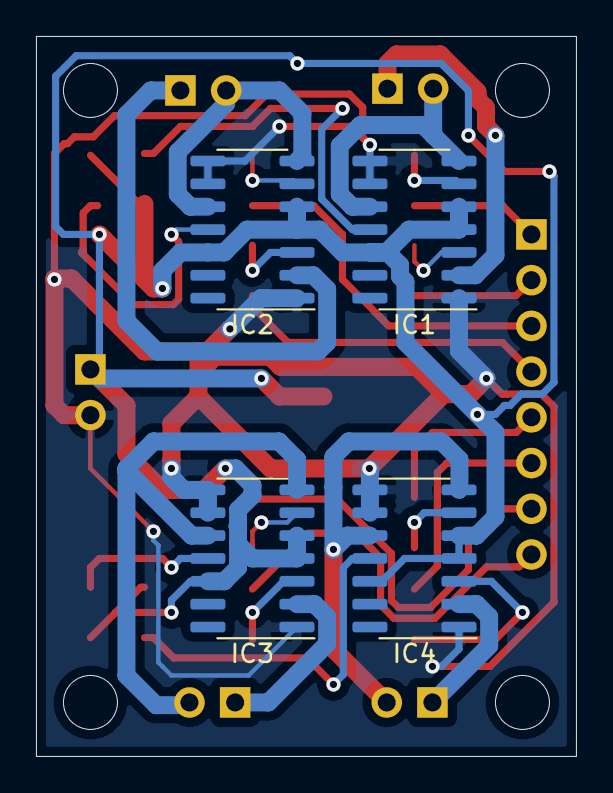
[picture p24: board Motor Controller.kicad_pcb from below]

Board: 2 copper layers, 30.0 x 40.0 mm, 23 parts (4 on the bottom side), 30 nets.

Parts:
C1: UUD1V331MNL1GS; CP_Elec_8x11.9
IC1, IC2, IC3, IC4: VNH7070ASTR; SOIC-14_3.9x8.7mm_P1.27mm
J1, J3, J4, J5, J6: Conn_01x02; PinHeader_1x02_P2.54mm_Vertical
J2: Conn_01x08_MountingPin; PinHeader_1x08_P2.54mm_Vertical
R1, R2, R3, R4, R5, R6, R7, R8, R9, R10, R11, R12: R_US; D_1206_3216Metric

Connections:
+12V: C1.1, IC1.4, IC1.5, IC1.12, IC2.4, IC2.5, IC2.12, IC3.4, IC3.5, IC3.12, IC4.4, IC4.5, IC4.12, J1.1, R1.1, R2.1, R11.2, R12.2
GND: C1.2, IC1.1, IC1.8, IC1.9, IC2.1, IC2.8, IC2.9, IC3.1, IC3.8, IC3.9, IC4.1, IC4.8, IC4.9, J1.2
unnamed: IC1.3, R4.1
unnamed: IC1.6, R3.1
unnamed: IC1.7, IC1.10, J3.2
unnamed: IC1.11, R1.2
unnamed: IC1.2, J3.1
unnamed: IC2.3, R6.1
unnamed: IC2.6, R5.1
unnamed: IC2.7, IC2.10, J4.2
unnamed: IC2.11, R2.2
unnamed: IC2.2, J4.1
unnamed: IC3.3, R7.2
unnamed: IC3.6, R8.2
unnamed: IC3.7, IC3.10, J5.2
unnamed: IC3.11, R11.1
unnamed: IC3.2, J5.1
unnamed: IC4.3, R9.2
unnamed: IC4.6, R10.2
unnamed: IC4.7, IC4.10, J6.2
unnamed: IC4.11, R12.1
unnamed: IC4.2, J6.1
unnamed: J2.1, R3.2
unnamed: J2.2, R4.2
unnamed: J2.3, R5.2
unnamed: J2.4, R6.2
unnamed: J2.5, R10.1
unnamed: J2.6, R9.1
unnamed: J2.7, R8.1
unnamed: J2.8, R7.1
